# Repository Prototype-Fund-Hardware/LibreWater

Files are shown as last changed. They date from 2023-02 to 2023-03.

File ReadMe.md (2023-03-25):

<!--
SPDX-FileCopyrightText: 2023 Terry Turtle <librewater@posteo.net>
SPDX-FileCopyrightText: 2023 inspyros <spyros@bluegreece.org>

SPDX-License-Identifier: CC-BY-SA-4.0
-->

# Acraea-Prototype

[](
    https://spdx.org/licenses/CERN-OHL-S-2.0.html)
[](
    https://creativecommons.org/licenses/by-sa/4.0/)
[](
    https://api.reuse.software/info/codeberg.org/LibreWater/Acraea-Prototype)

Acraea is a Small Scale Solar Desalination and Water Purification Prototype. \
It is powered by electric heating for scientific purpose
and for prototyping ahead according to the Libre Water Mission:

> Providing Free and Open Source Hardware Designs for Solar-thermal Desalination
> that can be manufactured and innovated locally in Makerspaces across the world

## License

Hardware and Firmware is licensed under the [CERN-OHL-S v2 license](
https://ohwr.org/cern_ohl_s_v2.txt)

Documentation is licensed under a
[Creative Commons Attribution-ShareAlike 4.0 International License](
https://creativecommons.org/licenses/by-sa/4.0/) \
This applies to all design files (CAD, BOM, etc.).

## Disclaimer

> THE DESIGN IS PROVIDED "AS IS", WITHOUT WARRANTY OF ANY KIND, EXPRESS OR
> IMPLIED, INCLUDING BUT NOT LIMITED TO THE WARRANTIES OF MERCHANTABILITY,
> FITNESS FOR A PARTICULAR PURPOSE AND NONINFRINGEMENT.
> IN NO EVENT SHALL THE AUTHORS OR RIGHT HOLDERS BE LIABLE FOR ANY CLAIM,
> DAMAGES OR OTHER LIABILITY,
> WHETHER IN AN ACTION OF CONTRACT, TORT OR OTHERWISE, ARISING FROM,
> OUT OF OR IN CONNECTION WITH THE DESIGN OR THE USE OR OTHER DEALINGS IN THE DESIGN.

## Acraea - Short Info

### Acraea is

- [x] a [fresh water Nymph](https://en.wikipedia.org/wiki/Acraea)
  from ancient Greek mythology.
- [x] a Small Scale Desalination and Water Purification Prototype
  that is powered by electric heating
  and has a built-in energy recovery using four stages.
- [ ] patented
- [x] [free (as in freedom) - so anyone can study, modify, distribute, make,
  and sell the design](https://www.oshwa.org/definition/)

### Version 2.0 of Acraea is

- [x] able to produce a limited amount of pure water from almost any water source
- [x] a Modular Design compatible for adaptation to solar-thermal
  and other heat sources
- [x] a Circular Design compatible for flexible mid-term design evolution
- [x] Compatible for modular scale-up

<p align="center">
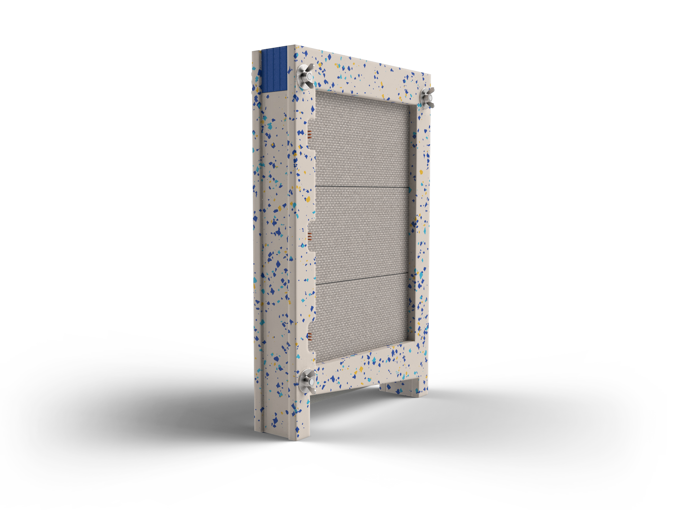
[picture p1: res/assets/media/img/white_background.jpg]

</br>
<b>Img.01:</b> Render of assembled Prototype
</p>

## Project Context

### This design is part of the Prototyping for LibreWater

### Mission of LibreWater

Providing Free and Open Source Hardware Designs for Solar-thermal Desalination
that can be manufactured and innovated locally in Makerspaces across the world

### Currently hosted by

Blue Greece - an Open Source Hardware Developer Collective

### Owned by

Turtles

### Here is a short intro video on Libre Water from a design contest in January 2023

<p align="center">
<a href="https://www.youtube.com/watch?v=Ojm_Nrax2sg" target="_blank">
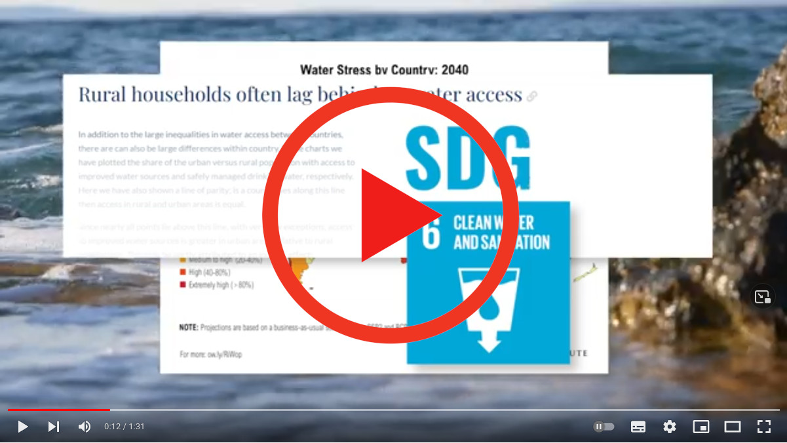
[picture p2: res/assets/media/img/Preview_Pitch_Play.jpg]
  
</a>
</p>

## Core Technology: Vertical Multiple-Effect-Distillation

The [process of the rain](
https://upload.wikimedia.org/wikipedia/commons/b/b1/Diagram_of_the_Water_Cycle.jpg)
in a box with integrated energy recovery.

Water is evaporated to clean steam and condensed again on an array of metal plates:
Creating highly pure water from almost any water source
without the need for special filters. #nofilter
The heat from the condensation process is recovered (_Img.04_)
and heating the next saltwater film for evaporation.

Check out a short video of the running module here:

<p align="center">
<a href="https://www.youtube.com/watch?v=kDWv2w7YqlU" target="_blank">
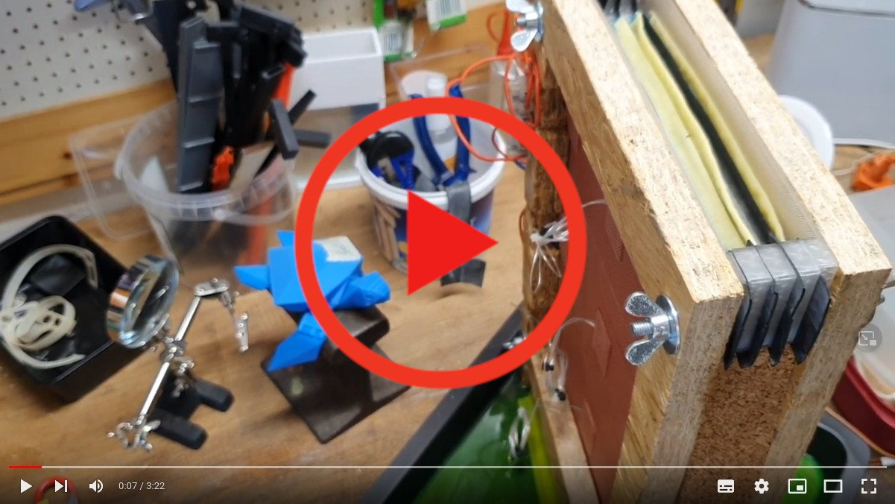
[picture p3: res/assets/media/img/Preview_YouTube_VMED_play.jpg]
  
</a>
</p>

<p align="center">
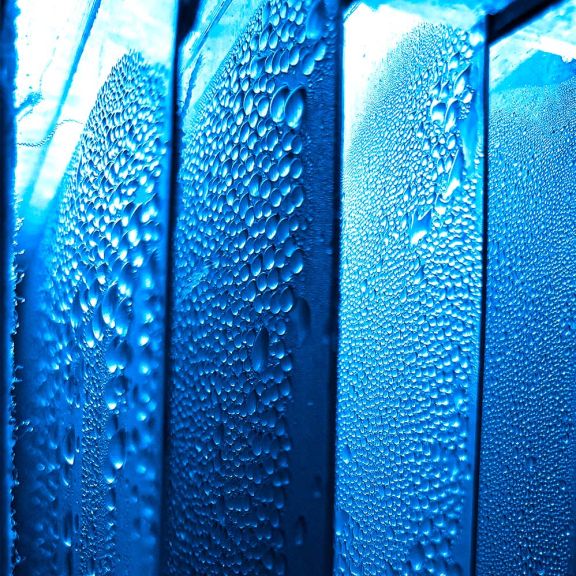
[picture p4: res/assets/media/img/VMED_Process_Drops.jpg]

</br>
<b>Img.03:</b>
Acraea 2.0 Running with removed sidewall.
Heating plate on left corner of the photograph.
Drops are growing from the condensation of pure steam.
</p>

<p align="center">
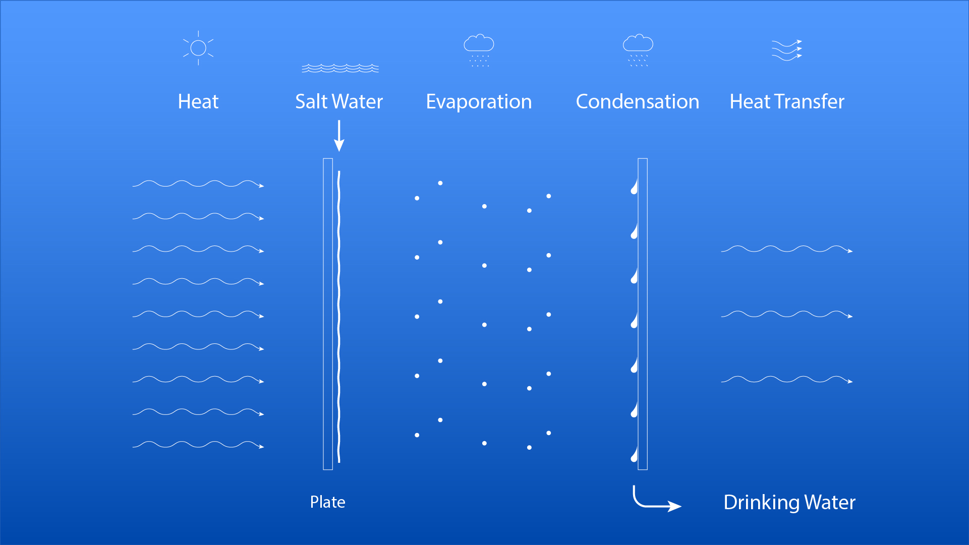
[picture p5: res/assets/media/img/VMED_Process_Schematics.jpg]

</br>
<b>Img.04:</b> Process Schematics:
The heat from condensation of fresh water is transferred ot the next stage
</p>

## Use-Cases: What is this prototype good for

### Makerspace Co-Creation

- Decentralized collaboration on design
- Accessible and fast iterations in early stage

### Research

- accessible setup for the functioning principle of Multiple-Effect-Distillation
- experimenting with heat transfer across plates and stages
- experimenting with fluid dynamics with different wicks or wick-free structures
- study behaviour of alternative materials & bio-materials

### Education

- simple production and assembly
- high responsiveness: fast start-up time
- uniting a broad field of disciplines: 3D Printing,
  CNC Milling, Sewing, Coding, Electronics
- familiarizing with Open Source Collaboration

## Modular Design Approach

Acraea has been designed with circularity and modularity in mind.
For the full part overview with more details,
check out the [Bill-Of-Materials](gen/bom.pdf).
For following our design choices and to bring in your own ideas,
please check out DesignPath.pdf (coming soon) <!-- TODO Add this file! -->

<p align="center">
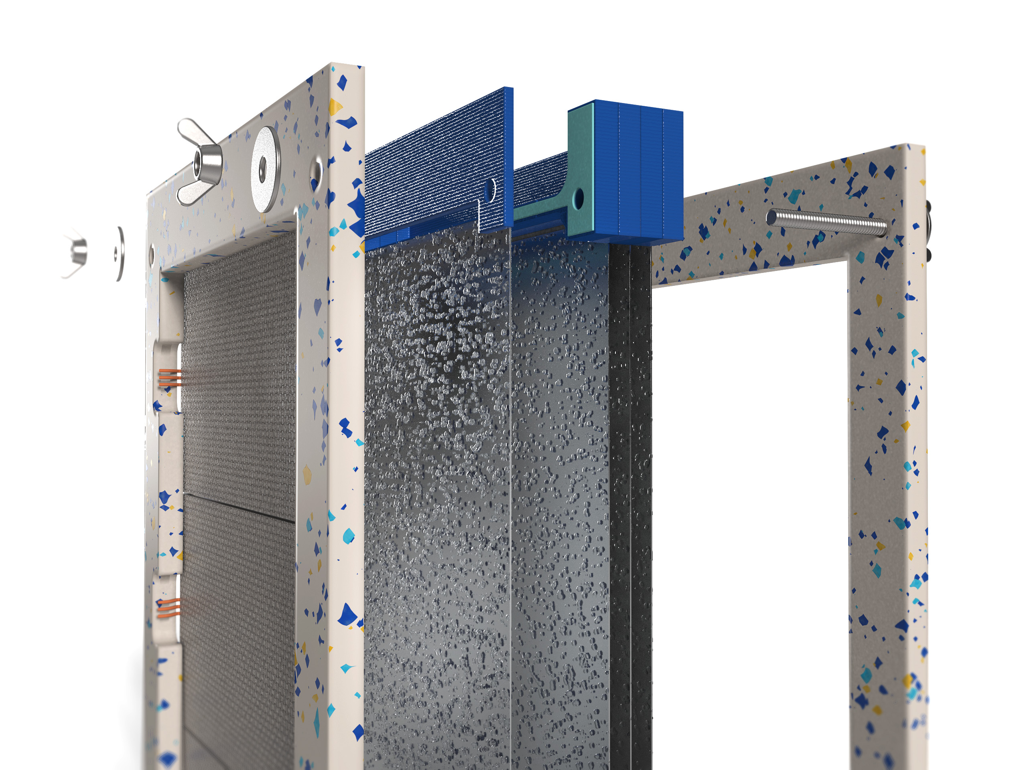
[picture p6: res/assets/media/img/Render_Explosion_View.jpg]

</br>
<b>Img.05</b>: Render: Explosion View
</p>

<p align="center">
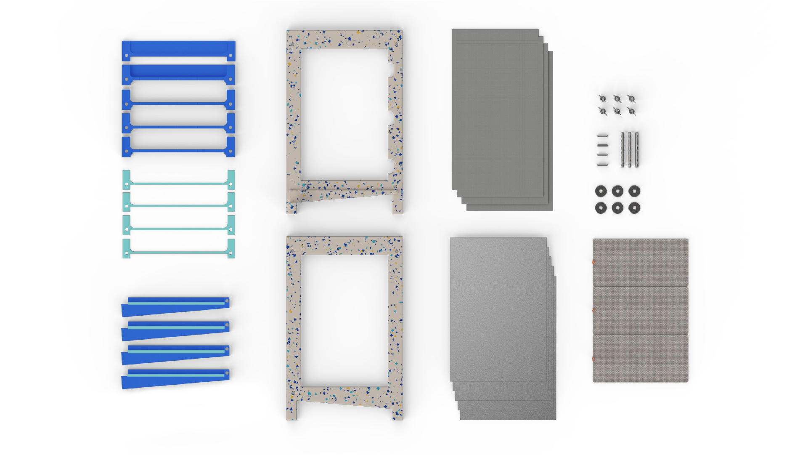
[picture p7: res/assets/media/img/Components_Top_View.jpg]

</br>
<b>Img.06:</b> Render: Top view of components
</p>

### Module: Casing

- CNC-Machined Plywood

### Module: Plates

- Plate size: 300 mm x 200 mm x 0,5 mm
- Plate Material: Aluminum

### Module: Heating

- Electric: 24V IPX7 Silicon Patches (note: currently still proprietary)

### Module: Fluid System

- Feed: FDM-Printed PETG
- Drainage: FDM-Printed PETG
- Sealing feed: Bicycle tube

## Manufacturing: Required tools & machinery

- 3D Printer (25 cm build size, e.g. Prusa i3)
- Sewing machine
- Jigsaw or CNC Mill
- basic workshop equipment

Please mind the time it takes to 3D-Print the PETG Parts:
one drainage can take about 3 hours;
the parts of the tank all together also 6 hours.

## Assembly

We are working on different approaches for assembly instructions.
We found the approach of OSH-AUTODOC to be most meaningful
and would be happy to hear your feedback.
Generally, we also provide How-To Videos on major releases.

### Assembly Manual

Follow the [Assembly Manual](gen/assembly/assembly-manual.pdf)
for Step-by-step instructions.
They were created with kind support of OSH-AUTODOC & JC. \
[OSH-AUTODOC](https://codeberg.org/osh-autodoc) is a FreeCAD Add-On under development,
to (semi) automatically generate documentation for Open Source Hardware. \
For more details, please contact JC or Pieter. <!-- TODO Add contact info/link! -->

<p align="center">
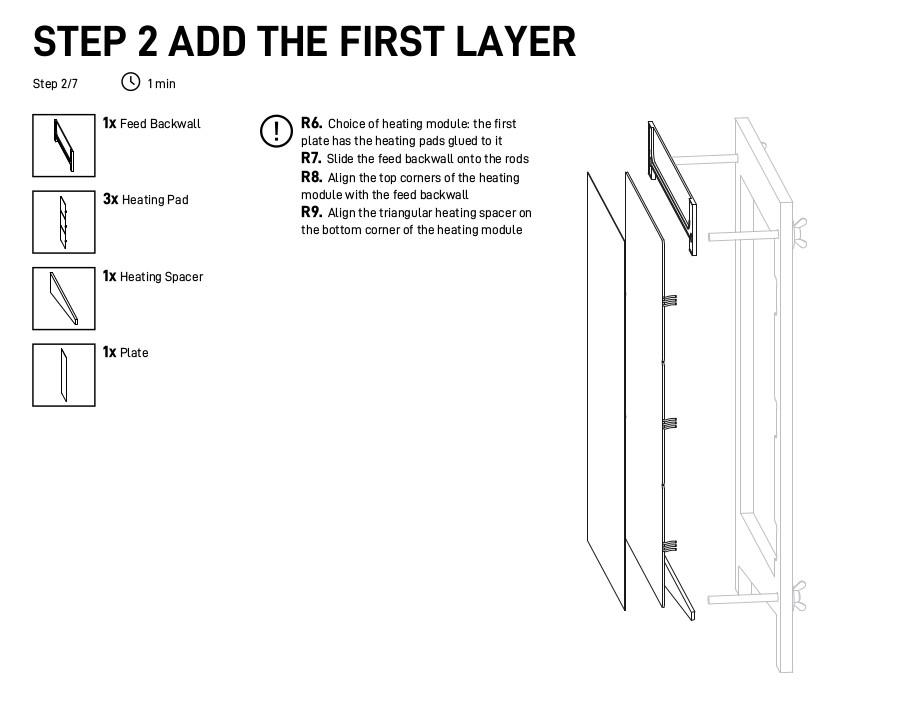
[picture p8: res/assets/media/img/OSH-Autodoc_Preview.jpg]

</br>
<b>Img.07:</b> Example of OSH-Autodoc generated assembly manual
</p>

### Videos

Stay tuned!
We are revising the video-assembly with the latest design update
and will share it shortly.
If you would like to engage and have ideas how to make clear and fun tutorials,
please reach out to us on <mailto:librewater@posteo.net>.

<p align="center">
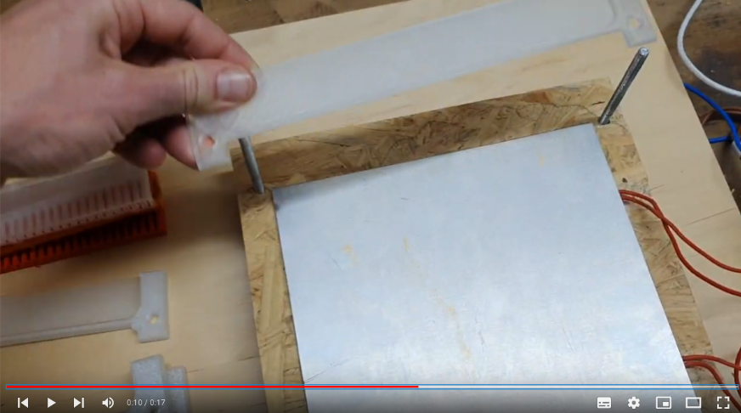
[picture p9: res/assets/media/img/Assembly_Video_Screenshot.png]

</br>
<b>Img.08:</b> Screenshot of How-To Assembly Video
</p>

### Process Control

### Heat input

The current approach is to have a constant power input of P = 150 W.
This is done by adjusting the On- and Off-switching times
by an Arduino or ESP32 controlled relay,
connected to a 24 V power supply which is powering three 24 V heating pads
on the first stage.

-> Check out the [Wiring instructions](gen/assembly/wiring.pdf)
for the setup and the code under [TurtleHeat_v3.ino](src/firmware/TurtleHeat.ino).

### Feed water input

The water level (hydrostatic pressure) in the tank
regulates the inflow of the non-drinkable water.
Filling it up to 2 cm creates maximum feed flow rate.
Testing & Validation
Vertical Multiple-Effect-Distillation is a simple process:
Quality and safety can be tested by electric conductivity with a TDS sensor.
Performance can be assessed by knowing the electric heat input
relative to the water output

<!-- TODO That file does not exist in the repo! -->
-> For more details, check out our Testing.md (draft stage)

## Research: Acraea for Open Science

Over the past 60 years, countless scientists and a few entrepreneurs
have worked on Solar-Powered Multiple-Effect-Distillation. \
One of the most recent reviews is from January 2022
by Lim et al. from Korea Institute of Machinery & Materials: \
[Designs and performance analysis of vertical multi-effect diffusion solar distiller:
A review - ScienceDirect (OpenAccess)](
https://www.sciencedirect.com/science/article/pii/S0011916422000273)

-> Check out selected sources and more info
in the Science Folder (soon) <!-- TODO Add this folder! -->

## Ideas for next Iterations

- [ ] Electric heating system: replace with locally producable alternative
- [ ] Adding a tank for longer operation
- [ ] Increase energy efficiency by adding more stages
- [ ] Testing an improved Wick design
- [ ] Testing Wick-Free designs
- [ ] Scaling Up
- [ ] Adding insulation
- [ ] Adding Solar-Thermal Heating Module

## Contact

Would you like to flow along?
Do you have any questions, ideas or general feedback?

For any inquiries, suggestions, collaborations or just spreading your love,
you may reach us at <mailto:librewater@posteo.net>.

<p align="center">
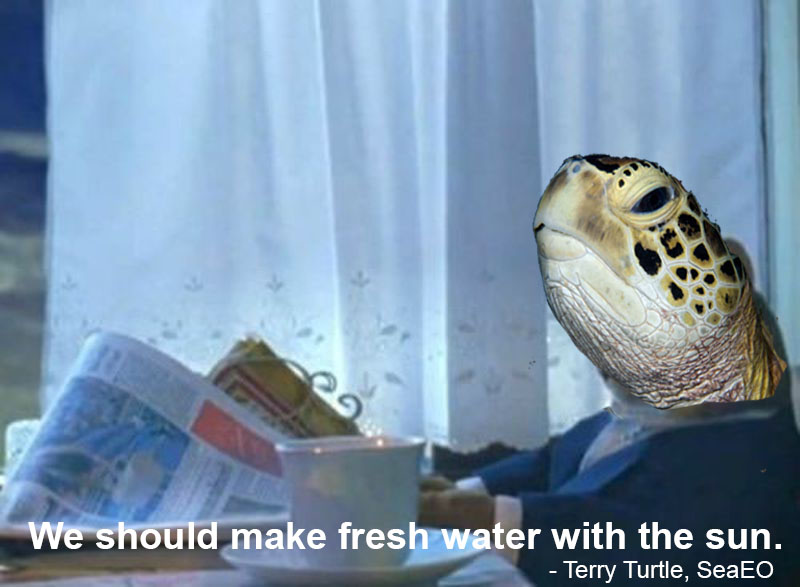
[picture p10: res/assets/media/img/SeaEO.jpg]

</br>
<b>Img.09:</b> Invitation from the SeaEO of LibreWater
</p>

## Related Open Source Hardware Projects

We thank Michael for his [Solar Pura](
https://www.appropedia.org/Solar_Pura:_High-efficiency_vertical_solar_still) work,
and Florian for his [MED Prototype](https://github.com/fsteckel/OpenWater).

## Contributions from Individuals

The list of contributors and supporters is endless.
What would be an appropriate way to mention all of them?
Is it meaningful to do so?
We are still thinking about how to give credit
and also give back in the best way. \
One thing is for sure:
Without the support of countless kind people from all over the world,
we would never have gone on this adventure.
You know who you are.
It has been most importantly your ideas, your feedback, our sharing of time -
often a little, sometimes a lot that has made this project a reality.

This is the magic of Open Source Hardware,
the magic of people joining together with collective intelligence.

## Support from Institutions and Spaces

In alphabetical order:

- [Bodossaki Foundation Social Dynamo](https://www.socialdynamo.gr/en/social-dynamo/)
  (Athens)
- [Curious Community Labs](https://curious.bio/) (Hamburg)
- [Fabulous St.Pauli](https://www.fablab-hamburg.org/) (Hamburg)
- [Fab City Hamburg](https://www.fabcity.hamburg) (Hamburg)
- [Hackerspace.gr](https://www.hackerspace.gr) (Athens)
- [Helidoni Foundation](https://www.helidonifoundation.org/) (Athens)
- [MIT Water Innovation Prize Semifinals](http://www.mitwaterinnovation.org/) (global)
- [Odyssea](https://odyssea.com) (Athens)
- [Open Hardware Makers](https://openhardware.space/) (global)
- [P2Plab](https://www.p2plab.gr/en/) (Greece)
- [Prototype Fund Hardware](https://hardware.prototypefund.de/) (Berlin)

## Safety Disclaimer

This design has not been tested extensively.
It has to be regarded as not yet suitable for:

- production of water for any other case other than scientific research
- Operation without supervision by a skilled operator
- Use in external environment

Please be aware that building a water machine can be dangerous
and requires full awareness of the risks involved.
Blue Greece/Libre Water does not warrant for any contents of the manual
and does not assume any risks whatsoever with regard to the contents of this manual
or the machine assembled by you.
Blue Greece/Libre Water further does not warrant for
and does not assume any risks whatsoever with regard to any parts of the machine
contained in this manual which are provided by third parties.
You need to have the necessary experience in handling the machinery
required to build the machine described in this manual.
Otherwise you should seek professional advice for building the machine.

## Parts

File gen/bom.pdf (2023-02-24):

Assembly number | Acraea 2.0
Part Name | Part Number | Thumbnail Image | Dimensions | Material | Quantity | Notes
| | | Module: Plates
Plate | P1 | 300 mm x 200 mm x 0,5 mm | Aluminum | 5

Thin aluminium can be
cut using a knife
| | Module: Fluid System
Feed Back Wall | F1 | (see part details) | PETG | 1
Feed Front Wall | F2 | (see part details) | PETG | 1
Sealing Feed | F3 | (see part details) | Bicycle Tube | 4 | Cut the wholes about 0,5 cm in from the distance of the rods for slight stretching
Feed Spacer | F4 | (see part details) | PETG | 3
Wick | F5 | 180 mm x 400 mm | Cotton Bedsheet (non-elastic) | 4 | The side corners are stabilized with a zig-zack cut. The the top corner is sewn over once at 0,5 cm
Drainage | F6 | (see part details) | PETG | 4

Sealing Drainage | F7 | (see part details) | WillowFlex
or similar | 4

Module: Casing

Casing Back Wall | C1 | (see part details) | MDF | 1
Washer | C2 | M 6 Outer diameter = 24 mm | Stainless Steel | 6
Thumbscrew | C3 | M6 | Stainless Steel | 6
Threaded Rod | C4 | M6 100 mm | Stainless Steel | 3
Casing Right Wall | C5 | (see part details) | Cork | 1
Casing Front Wall | C6 | (see part details) | Cork | 1
Casing Left Wall A | C7 | (see part details) | Cork | 1

Casing Left Wall B | C8 | (see part details) | MDF | 1

Module: Heating

24V IPX7 Heating Pad (P= 200W) | H1 | 200 mm x 100 mm | Silicon | 3
Heating Spacer | H2 | (see part details) | Wood | 1
24 V DC Power Supply (P = 750W) | H3 | - | | 1
ESP32 | H4 | - | | 1
Micro USB Cable | H5 | - | | 1
5 V USB Power Supply | H6 | - | | 1
4 Channel Relay | H7 | - | | 1

Luster Terminals | H8 | - | 8
Jumper Wires | H9 | - | 10
Standard Copper cables 2-Wire (1,5 mm²) | H10 | 10m | 1
230 V Plug and 3-Wire cable | H11 | 2m | 1
Breadboard compatible with ESP32 | H12 | - | 1

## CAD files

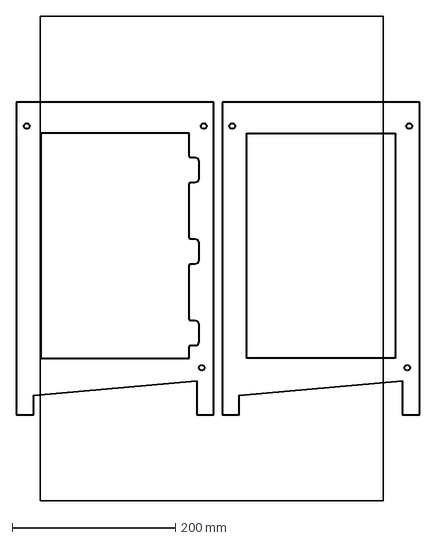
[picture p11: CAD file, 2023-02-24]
gen/mechanical/2d/casing_cnc.dxf
494.1 x 594.1 mm

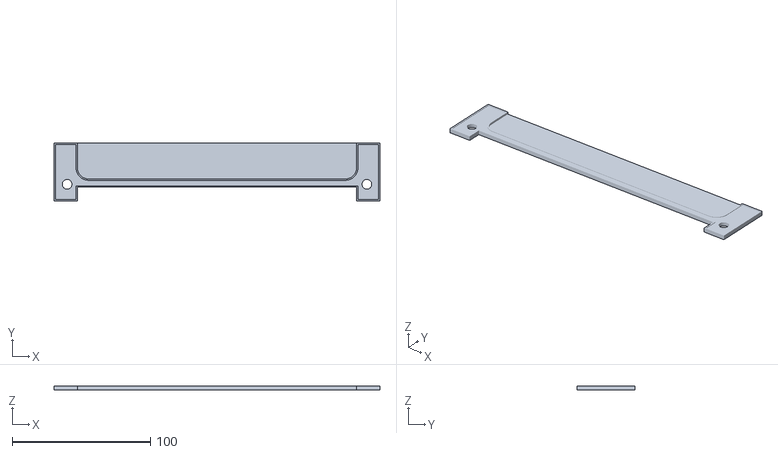
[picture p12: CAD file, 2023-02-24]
gen/mechanical/3d-print/feed-backwall.stl
236.0 x 42.0 x 3.19

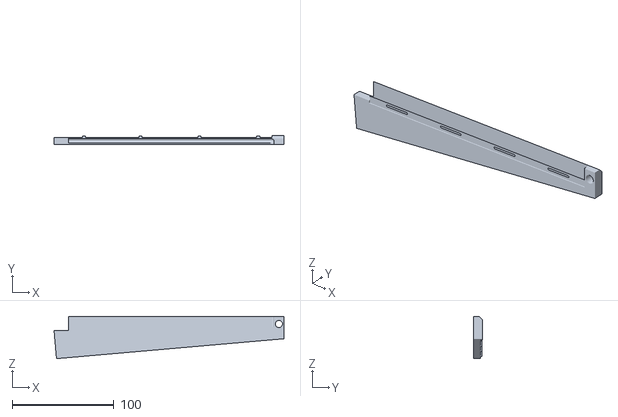
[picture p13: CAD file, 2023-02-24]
gen/mechanical/3d-print/drainage.stl
226.0 x 8.50 x 41.6

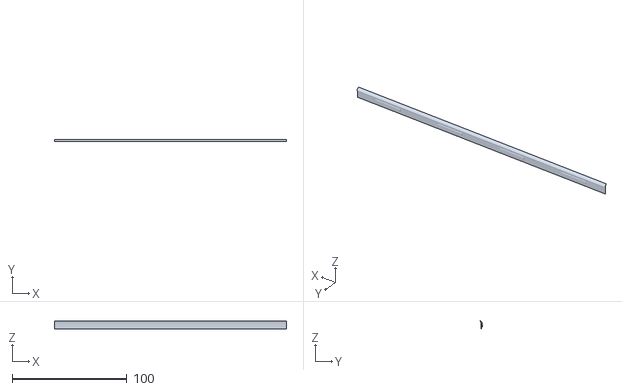
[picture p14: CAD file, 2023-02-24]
gen/mechanical/3d-print/drainage-sealing.stl
202.0 x 1.96 x 7.11

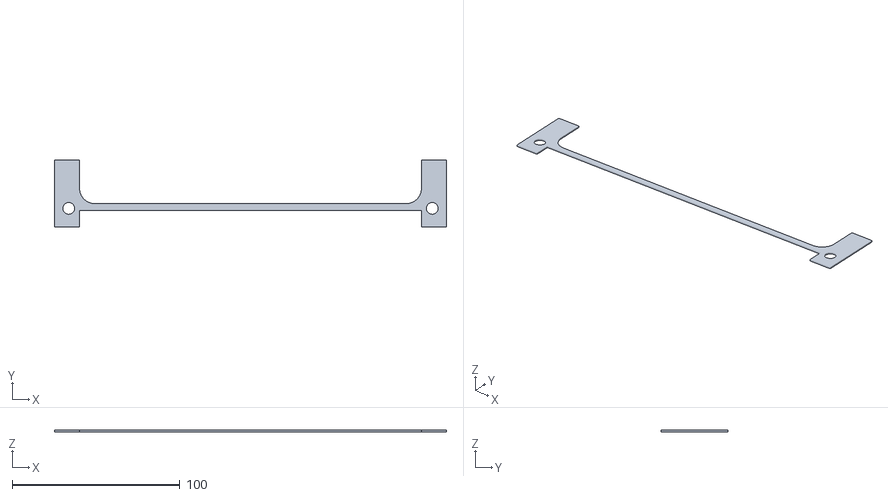
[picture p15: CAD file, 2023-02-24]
gen/mechanical/3d-print/feed-sealing.stl
234.0 x 40.0 x 1.00

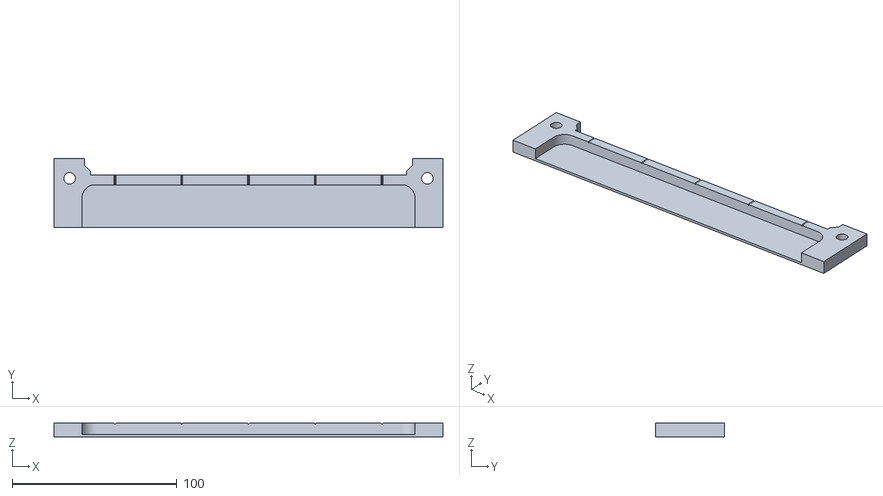
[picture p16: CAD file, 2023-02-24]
gen/mechanical/3d-print/feed-frontwall.stl
236.0 x 42.0 x 8.20

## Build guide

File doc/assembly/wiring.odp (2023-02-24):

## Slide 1

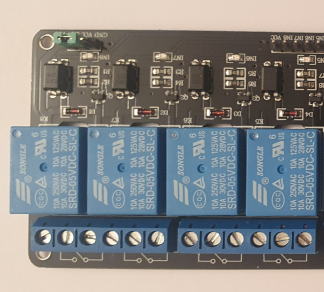
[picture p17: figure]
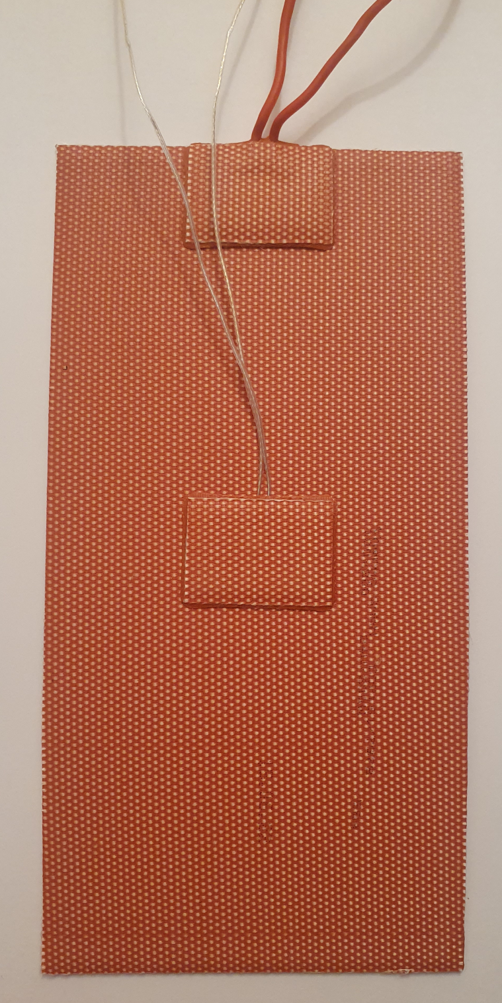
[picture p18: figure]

Acraea 2.0 Heating Module Wiring v0.1

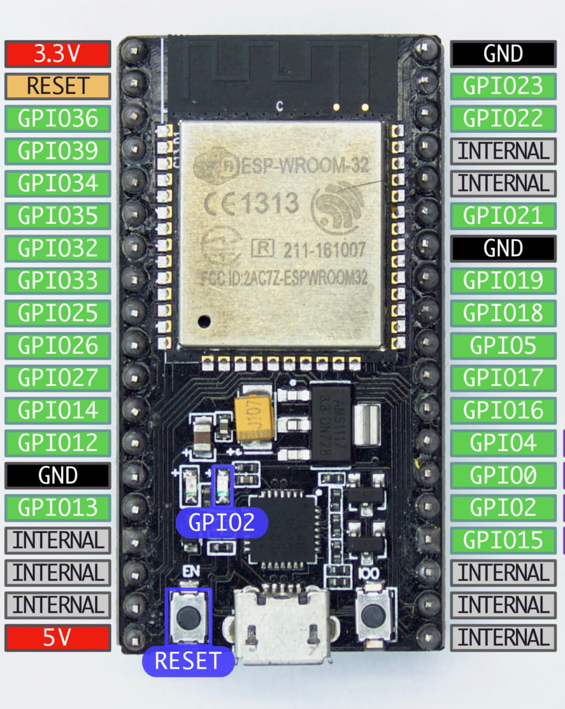
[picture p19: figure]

5V

GND

IN1

IN2

IN3

4-Channel Relay

ESP32

5 V USB Power Supply

230 V AC

L

230 V AC

N

230 V AC

GND

750 W

Power Supply

24 V DC

+

24 V DC

Wall

Plug

ThermoTech

IPX7

Silicon Heating Pad 200 W

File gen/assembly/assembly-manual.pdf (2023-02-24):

# ACRAEA 2.0 ASSEMBLY MANUAL

# Step by Step Instructions

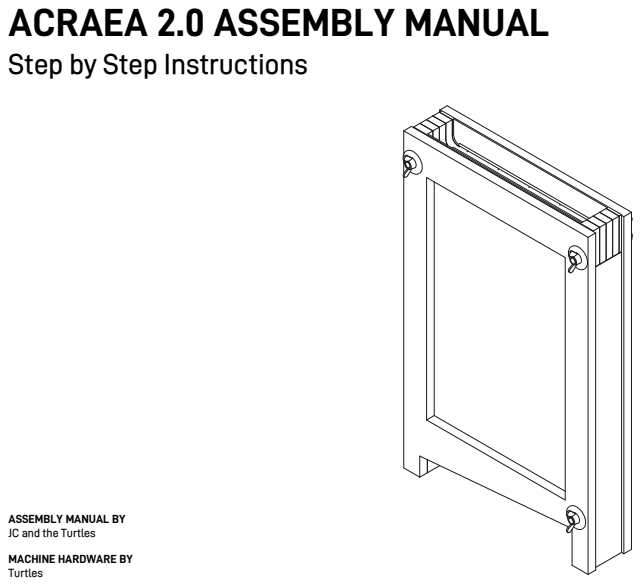
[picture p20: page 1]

ASSEMBLY MANUAL BY
JC and the Turtles

MACHINE HARDWARE BY
Turtles

# INDEX

Step 1 Get the Backframe Ready | 3
Step 2 Add the first layer | 4
Step 3.1 Add the wick | 5
Step 3.2 Add the feed spacer | 6
Step 3.3 Add drainage and sealing | 7
Step 3.4 Add the plate | 8
Step 4 Repeat step 3 Twice | 9
Step 5.1 Add the last wick and drainage | 10
Step 5.2 Add the top feed spacer and plate | 11
Step 6 Add the sidewall and the top frame | 12
Step 7 Close the module | 13

Acraea 2.0 - 2

# STEP 1 GET THE BACKFRAME READY

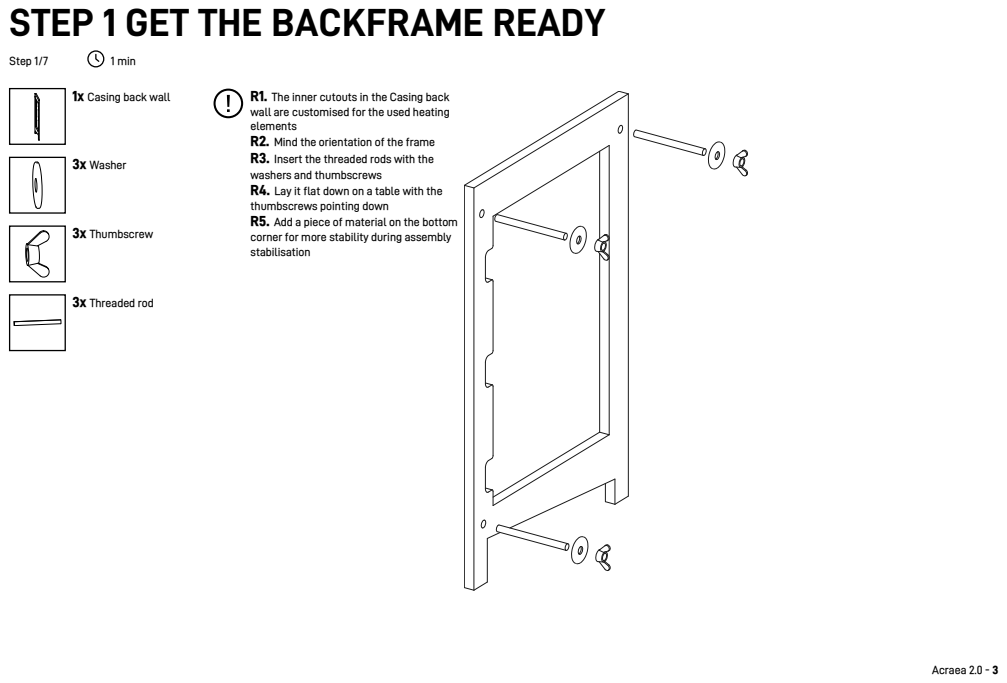
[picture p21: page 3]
Step 1/7; 1 min; 3x Washer; 3x Thumbscrew; 3x Threaded rod

1x Casing back wall

R1. The inner cutouts in the Casing back
wall are customised for the used heating
elements
R2. Mind the orientation of the frame
R3. Insert the threaded rods with the
washers and thumbscrews
R4. Lay it flat down on a table with the
thumbscrews pointing down
R5. Add a piece of material on the bottom
corner for more stability during assembly
stabilisation

# STEP 2 ADD THE FIRST LAYER

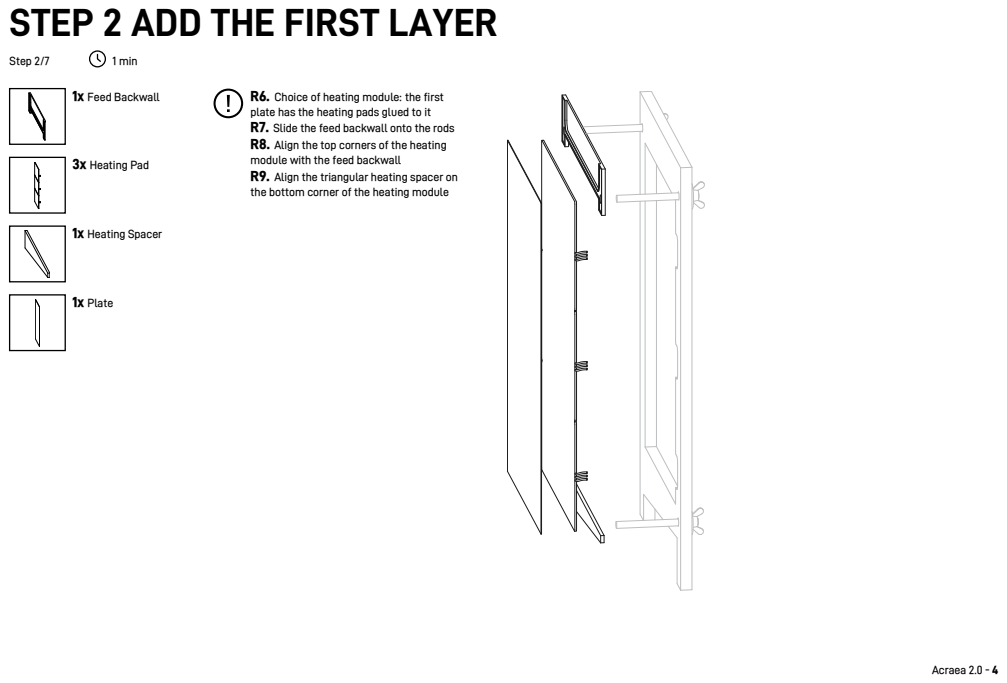
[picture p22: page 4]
Step 2/7; 1 min; 1x Feed Backwall; 3x Heating Pad; 1x Heating Spacer; 1x Plate

R6. Choice of heating module: the first
plate has the heating pads glued to it
R7. Slide the feed backwall onto the rods
R8. Align the top corners of the heating
module with the feed backwall
R9. Align the triangular heating spacer on
the bottom corner of the heating module

# STEP 3.1 ADD THE WICK

### Correction: Skip this step - see next step

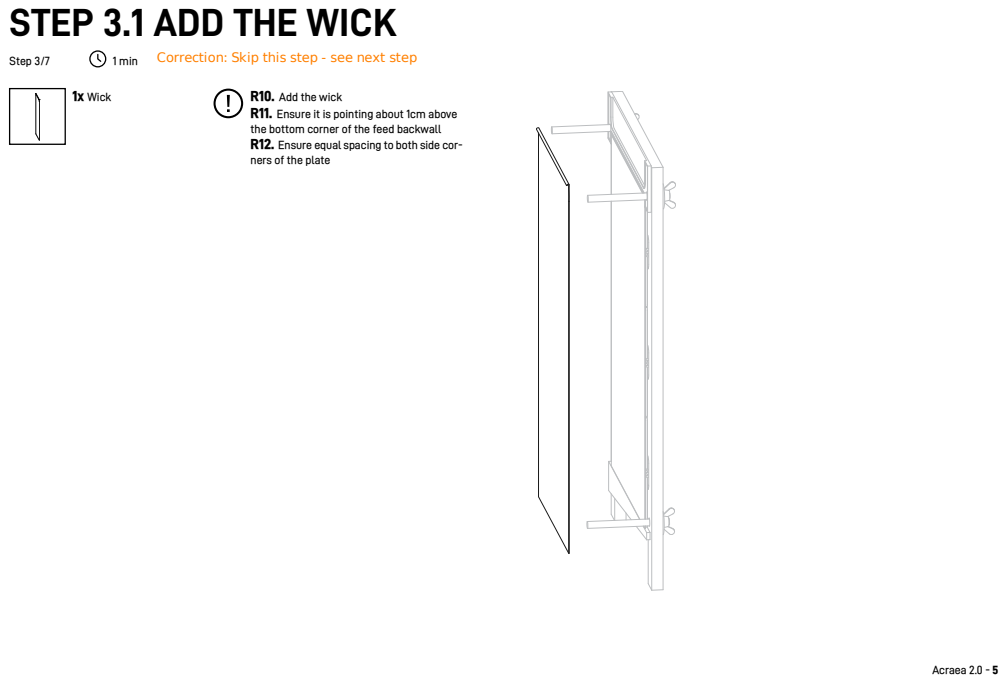
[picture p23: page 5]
Step 3/7; 1 min; 1x Wick; R10. Add the wick

R11. Ensure it is pointing about 1cm above
the bottom corner of the feed backwall
R12. Ensure equal spacing to both side cor-
ners of the plate

# STEP 3.2 ADD THE FEED SPACER

### Correction: Step 3.1 happens after .R13

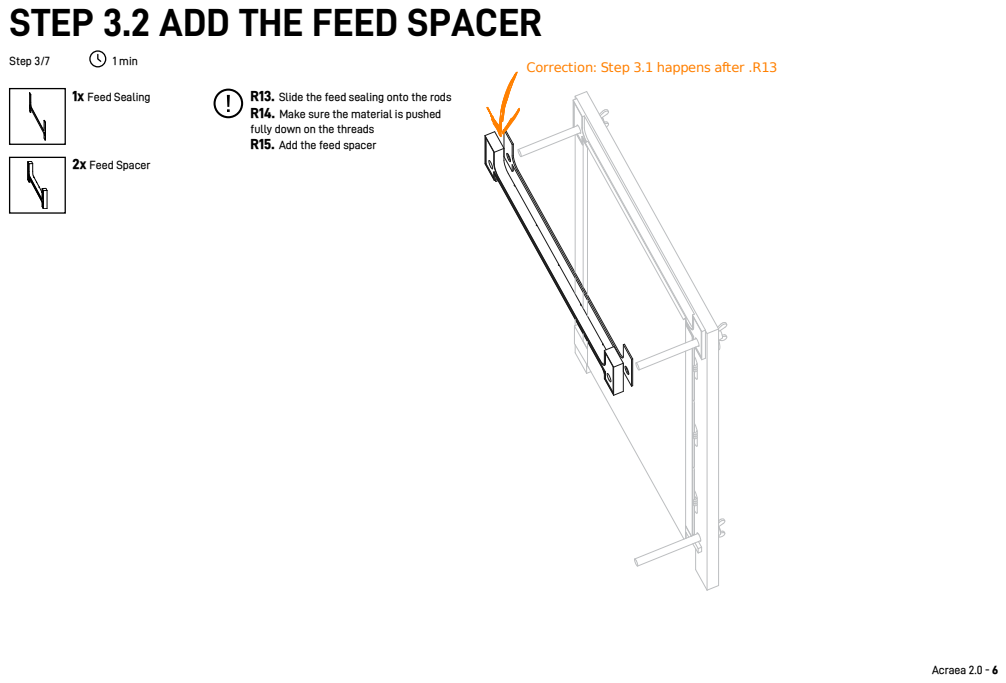
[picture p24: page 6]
Step 3/7; 1 min; 1x Feed Sealing; 2x Feed Spacer

R13. Slide the feed sealing onto the rods
R14. Make sure the material is pushed
fully down on the threads
R15. Add the feed spacer

# STEP 3.3 ADD DRAINAGE AND SEALING

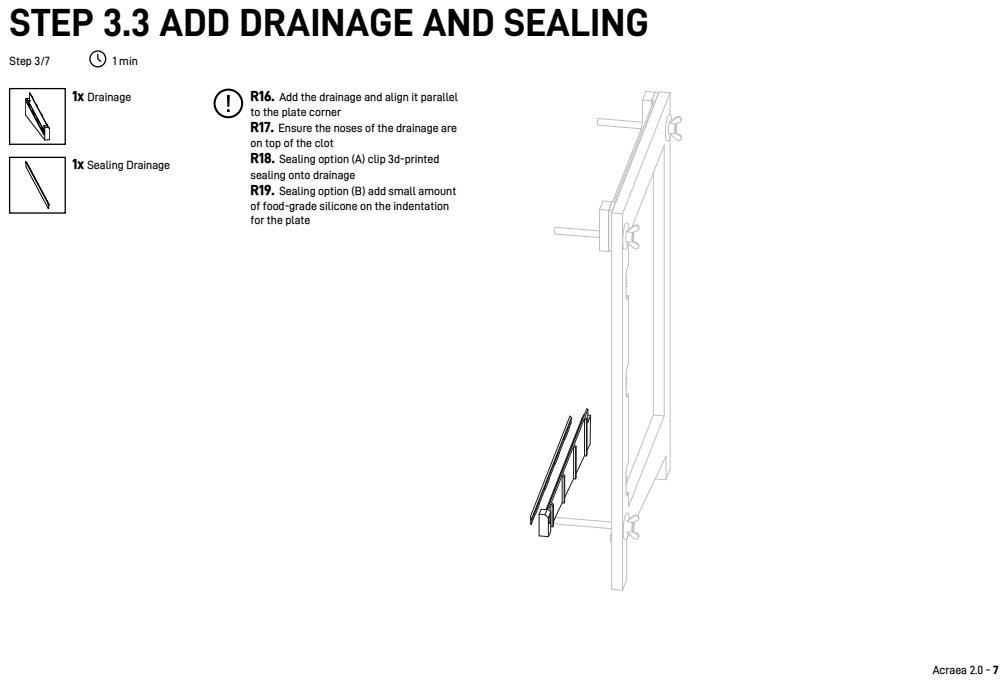
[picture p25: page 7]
Step 3/7; 1 min; 1x Drainage; 1x Sealing Drainage

R16. Add the drainage and align it parallel
to the plate corner
R17. Ensure the noses of the drainage are
on top of the clot
R18. Sealing option (A) clip 3d-printed
sealing onto drainage
R19. Sealing option (B) add small amount
of food-grade silicone on the indentation
for the plate

# STEP 3.4 ADD THE PLATE

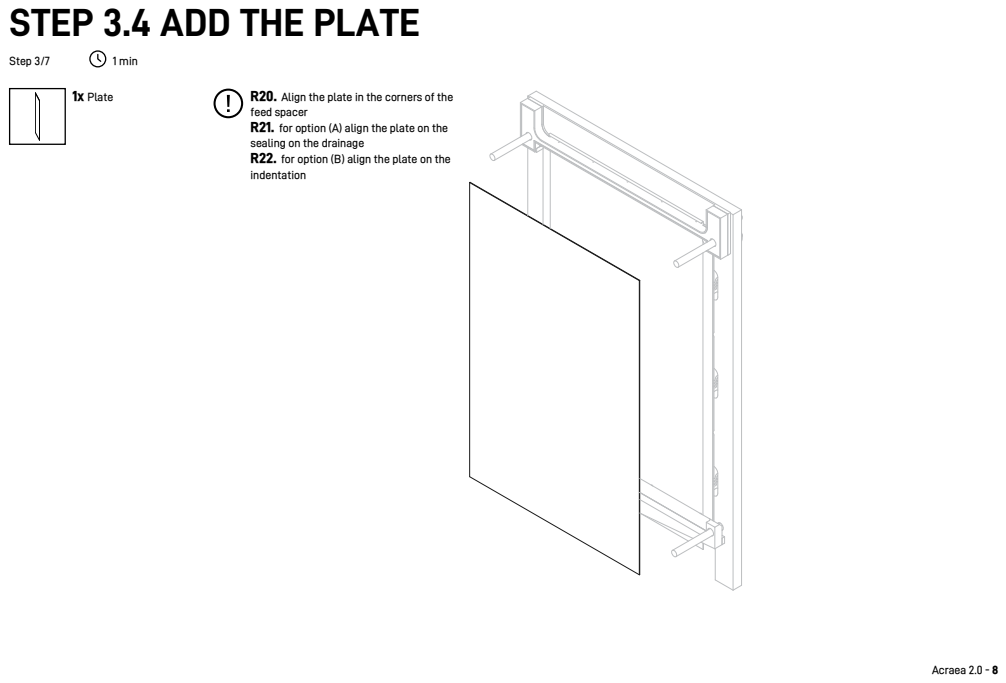
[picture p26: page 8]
Step 3/7; 1 min; 1x Plate; R20. Align the plate in the corners of the

feed spacer
R21. for option (A) align the plate on the
sealing on the drainage
R22. for option (B) align the plate on the
indentation

# STEP 4 REPEAT STEP 3 TWICE

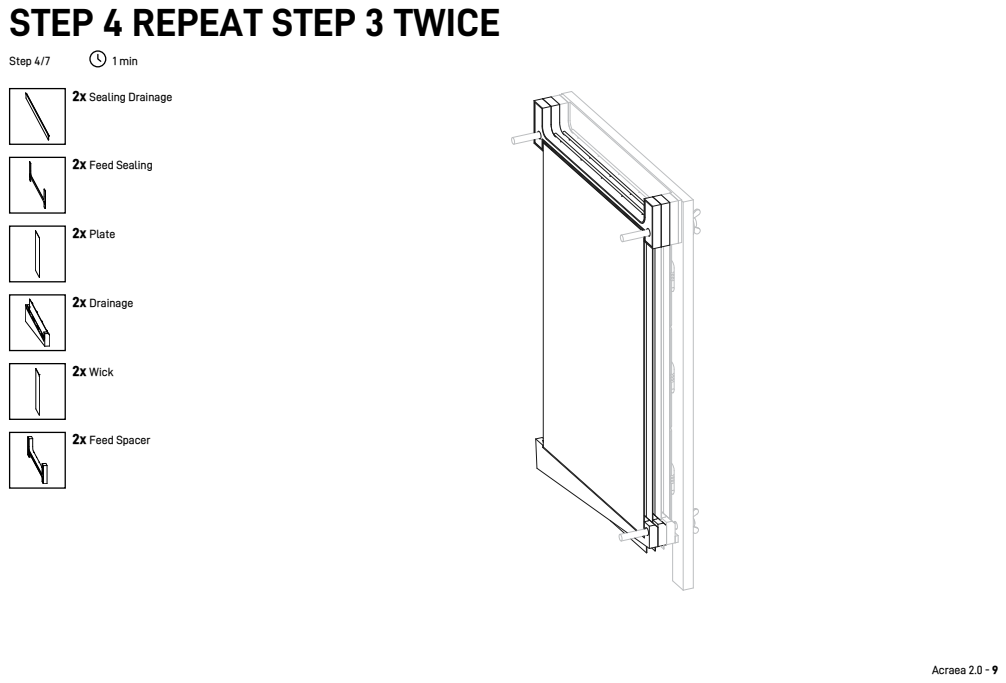
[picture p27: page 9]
Step 4/7; 1 min; 2x Sealing Drainage; 2x Feed Sealing; 2x Plate; 2x Drainage; 2x Wick; 2x Feed Spacer

# STEP 5.1 ADD THE LAST WICK AND DRAINAGE

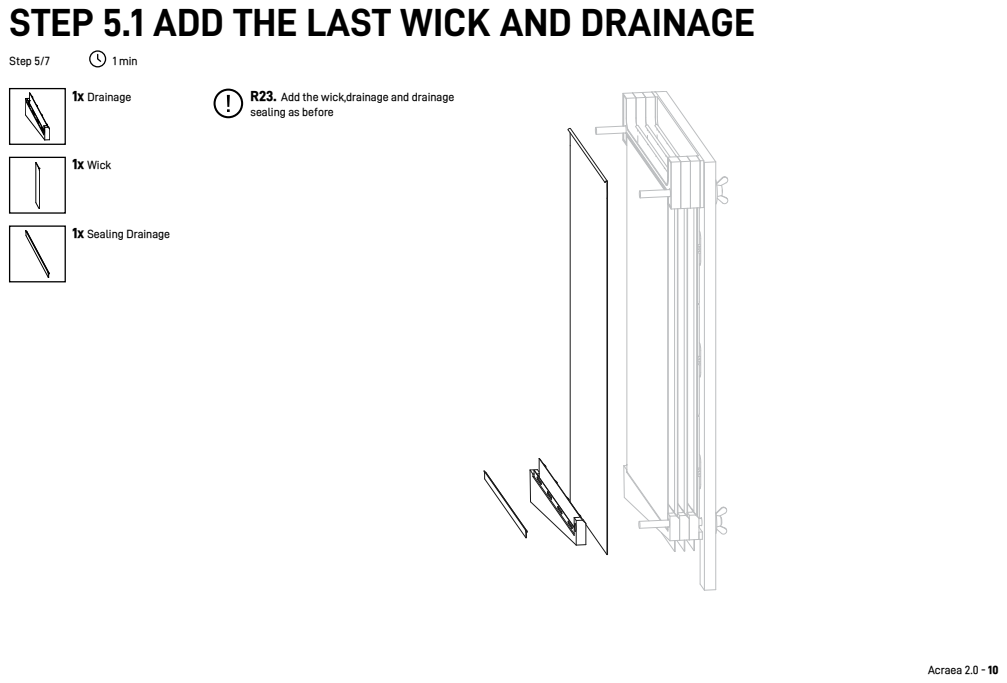
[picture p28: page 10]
Step 5/7; 1 min; 1x Drainage; 1x Wick; 1x Sealing Drainage

R23. Add the wick,drainage and drainage
sealing as before

# STEP 5.2 ADD THE TOP FEED SPACER AND PLATE

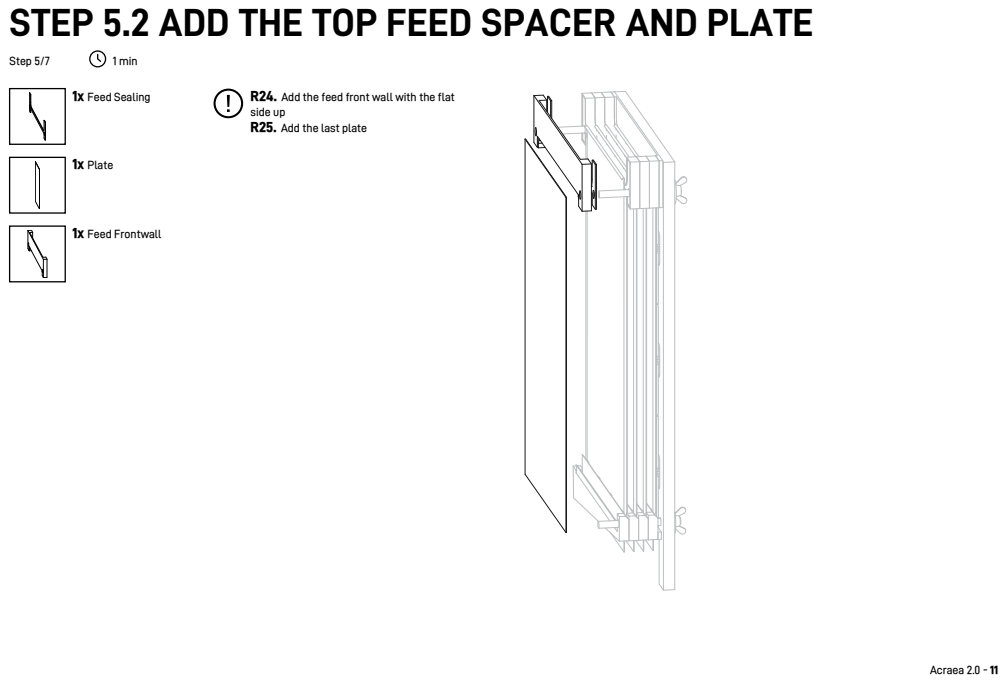
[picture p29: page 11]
Step 5/7; 1 min; 1x Feed Sealing; 1x Plate; 1x Feed Frontwall

R24. Add the feed front wall with the flat
side up
R25. Add the last plate

# STEP 6 ADD THE SIDEWALL AND THE TOP FRAME

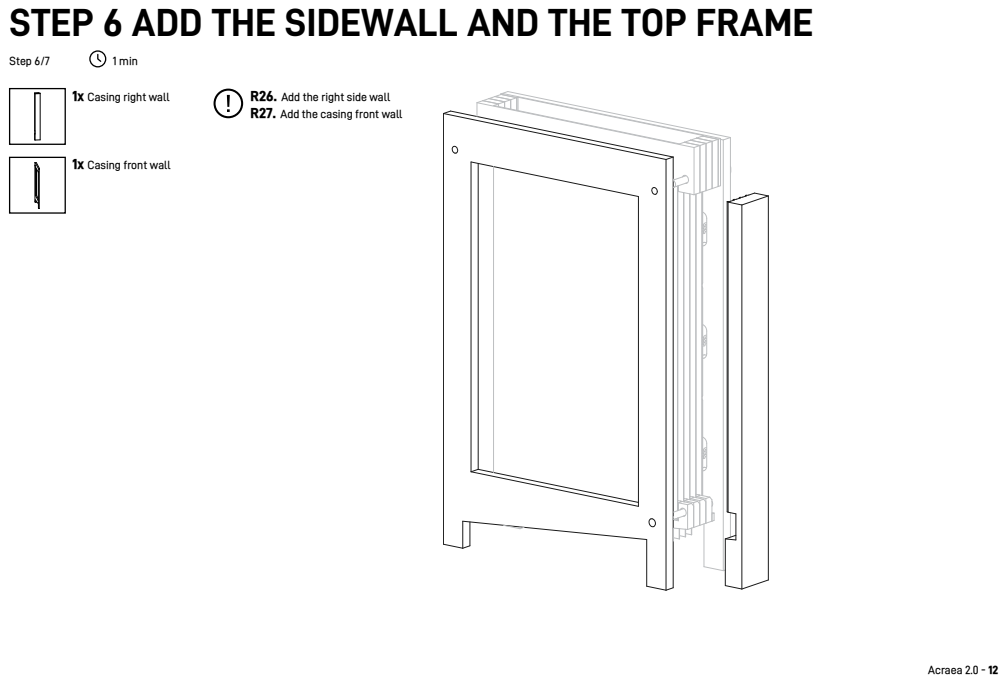
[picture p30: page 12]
Step 6/7; 1 min

1x Casing right wall

R26. Add the right side wall
R27. Add the casing front wall

1x Casing front wall

# STEP 7 CLOSE THE MODULE

Step 7/7 | 1 min

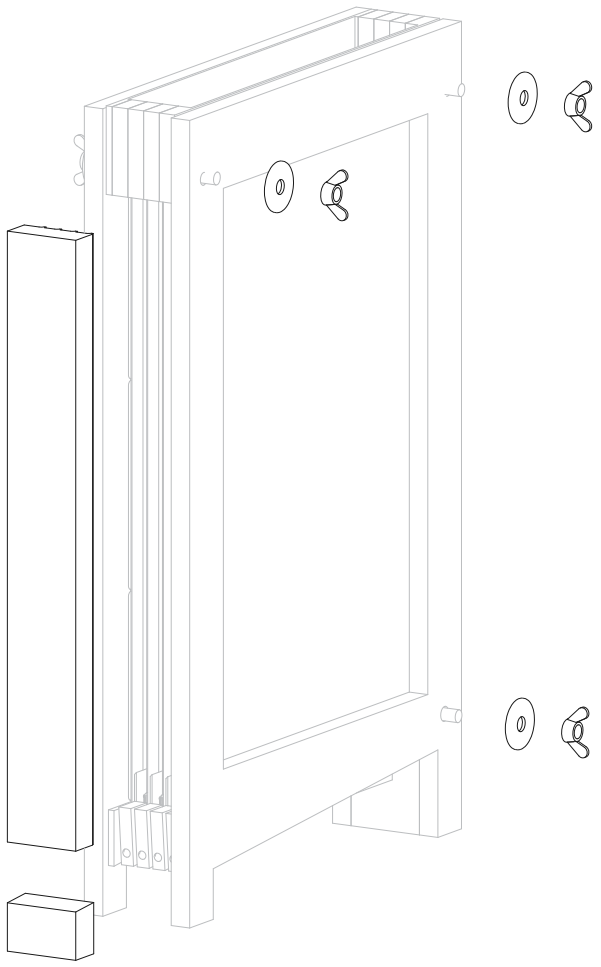
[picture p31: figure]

| 3x Washer

1x Casing left wall A

3x Thumbscrew

1x Casing left wall B

## R28. Add the casing left wall A and B

## R29. Close the module by tightening the bolts equally to a medium strength (like closing a plastic bottle)

R30. Pull down the cloths to stretch them nicely.

## - If it is to hard to pull, loosen the bolts slightly - If the cloth is not grabbed well, tighten the bolts slightly

## R40. Inspect the Stages thoroughly using a torch

The Wicks have to be all be flat down on the plates.
At no point, not even with a lint, touch the other side. This will contaminate your pure water side.
Finally: Tighten all the thumbscrews on both sides well.

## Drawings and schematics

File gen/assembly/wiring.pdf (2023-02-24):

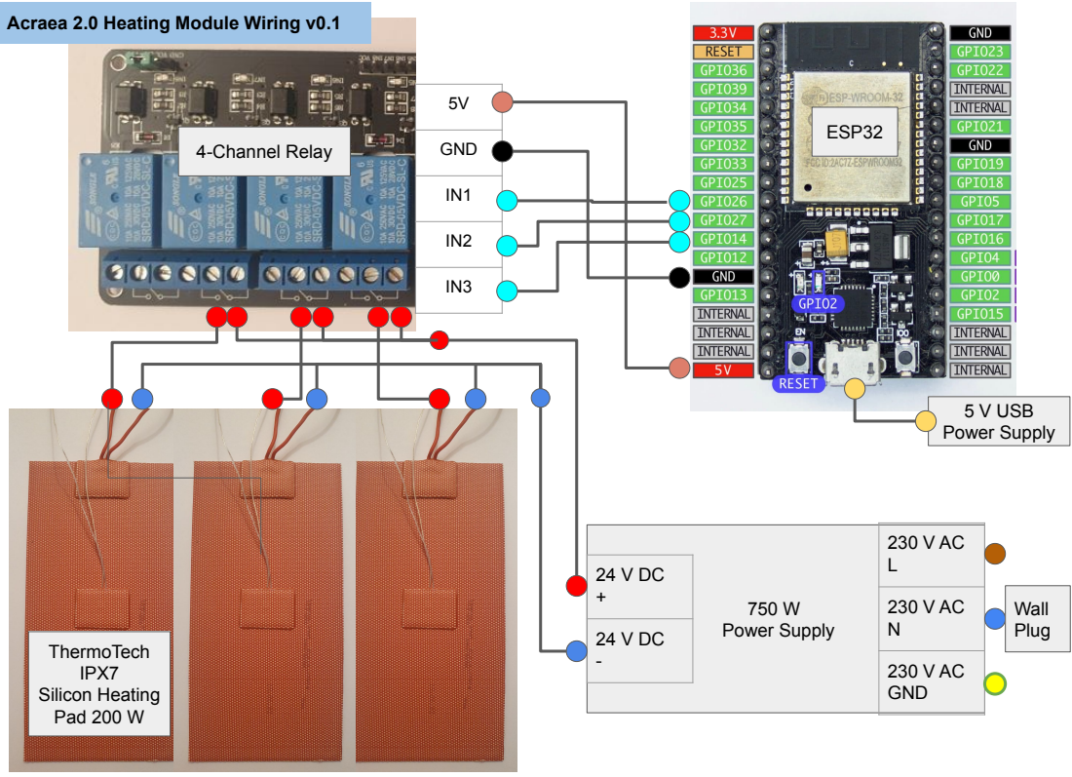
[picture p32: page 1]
750 W Power Supply; 230 V AC GND; GND; 5 V USB Power Supply; Wall Plug; ESP32; 4-Channel Relay; ThermoTech IPX7 Silicon Heating Pad 200 W

Acraea 2.0 Heating Module Wiring v0.1

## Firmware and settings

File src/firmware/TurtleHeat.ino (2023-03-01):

// SPDX-FileCopyrightText: 2023 Terry Turtle <librewater@posteo.net>
// SPDX-FileCopyrightText: 2023 inspyros <spyros@bluegreece.org>
//
// SPDX-License-Identifier: CERN-OHL-S-2.0

// assigning variables to the digital pins on the arduino board
const int RELAY_1 = 27;
const int RELAY_2 = 14;
const int RELAY_3 = 12;
const unsigned long ONTIME = 2100;
const unsigned long OFFTIME = 700;
const unsigned long MEANINGOFLIFE = 42;

// ESP32
// 3 pcs ThermoTech 200mm x 100 mm (P_max = 200 W each)
// ONTIME and OFFTTIME are activated for one module at a time and in a continuous loop: Heating Pad 1, Heating Pad 2, Heating Pad 3, Heating Pad 1, etc

// P = 200 W ONTIME = 2000 OFFTIME = 0
// P = 150 W ONTIME = 2100 OFFTIME = 700
// P = 100 W ONTIME = 2000 OFFTIME = 2000
//e.g.: ONTIME = 2100 ms and OFFTIME =  700 ms will lead to an average overall P = ONTIME/(ONTIME+OFFTIME)*P_max = 150 W

void setup() {
  // initialize digital pins as an output.
  pinMode(RELAY_1, OUTPUT);
  pinMode(RELAY_2, OUTPUT);
  pinMode(RELAY_3, OUTPUT);
}

void loop() {

  // heating pad 1
  digitalWrite(RELAY_3, LOW);
  digitalWrite(RELAY_1, HIGH);
  delay(ONTIME);
  digitalWrite(RELAY_1, LOW);
    delay(OFFTIME);

  // heating pad 2
  digitalWrite(RELAY_1, LOW);
  digitalWrite(RELAY_2, HIGH);
  delay(ONTIME);
    delay(OFFTIME);

  // heating pad 3
  digitalWrite(RELAY_2, LOW);
  digitalWrite(RELAY_3, HIGH);
  delay(ONTIME);
     digitalWrite(RELAY_3, LOW);
     delay(OFFTIME);
}

// sources used: https://arduinogetstarted.com/tutorials/arduino-relay

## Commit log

2023-02-23 Adding res (ressource) folder
    resources: asssets (e.g. images used from others), media (e.g. own images), configuration files (like for 3d printing),
2023-02-24 Upload 3d-print files only as STL (from acrea-2.0.step)
    [acraea-2.0-drainage-sealing.stl, acraea-2.0-drainage.stl, acraea-2.0-feed-backwall.stl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]
2023-02-24 Upload of code for Arduino/ESP32+Relay controlled electric heating
2023-02-24 Upload Bill Of Material (BOM)
    [bom.ods]
2023-02-24 Upload Assembly Manual for Acraea 2.0 (supported by OSH-AUTODOC)
    codeberg.org/osh-autodoc
2023-02-24 Upload of wiring instructions for electric heating system
2023-02-24 Upload of DXF file for CNC Machined Frame
    [Acraea 2.0_Casing_CNC.dxf]
2023-02-24 Upload Youtube Pitch Preview
2023-02-24 Upload Pitch Preview
2023-02-27 Update 'README.md'
    introducing <br /> in the assembly and research part
2023-02-28 Uploaded editable CAD file
    (sorry, it is currently in Shapr3D Format)
2023-03-01 Moves generated files to dir `gen`
    .... and removes version number and project name
    from these file names
    [casing_cnc.dxf, drainage-sealing.stl, drainage.stl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]
2023-03-01 Fixes Licensing - Now REUSE compliant
    [TurtleHeat.ino]
2023-03-01 Fixes bom.pdf location
2023-03-23 Adds scripts to generate bom.csv and wiring.pdf using LibreOffice

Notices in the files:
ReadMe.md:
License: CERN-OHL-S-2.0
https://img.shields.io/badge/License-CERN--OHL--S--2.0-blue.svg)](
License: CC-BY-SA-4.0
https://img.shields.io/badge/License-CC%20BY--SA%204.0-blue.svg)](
